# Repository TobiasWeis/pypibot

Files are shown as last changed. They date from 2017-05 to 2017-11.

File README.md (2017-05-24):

# PyPiBot

A robot that is controlled by python on a raspberry pi.
The build is rover-like, with four driven wheels.

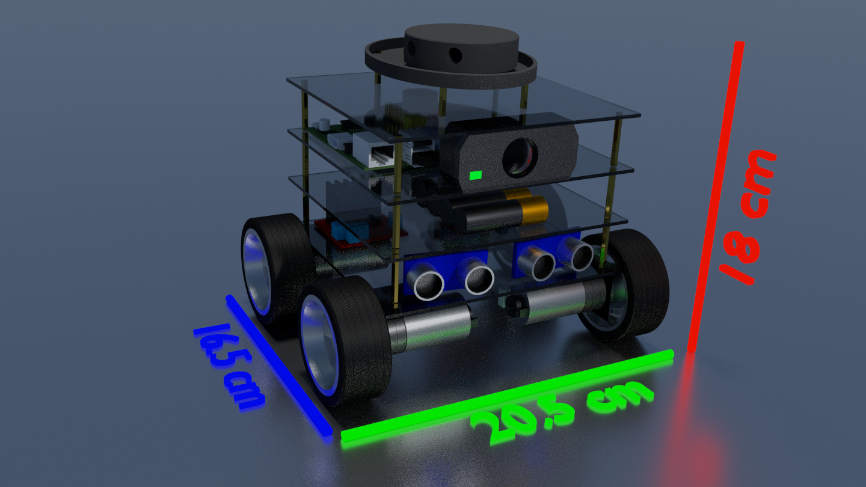
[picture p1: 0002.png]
PyPiBot

<!-- ![PyPiBotGif](./docs/bot.gif) -->

## Parts-List
Whenever available, detailed information and supplier-link are provided as pdf in the docs-folder.
* Raspberry-Pi B+ V2
* Edimax EW-7811UN Wireless USB Adapter

* Motors: 4x DC 6.0V, 35:1 gear ratio, diameter of shaft: 4mm
* Motor-mounts: 4x DROK 25mm universal dc motor mount
* Motor-driver: 2x L298 dual H-bridge modules

* Tires: 4x GoolRC 1:10 Drift Car Tires
* Tire-mount: 12mm Hex Wheel Adapter for 4mm shaft

Current hardware configuration:
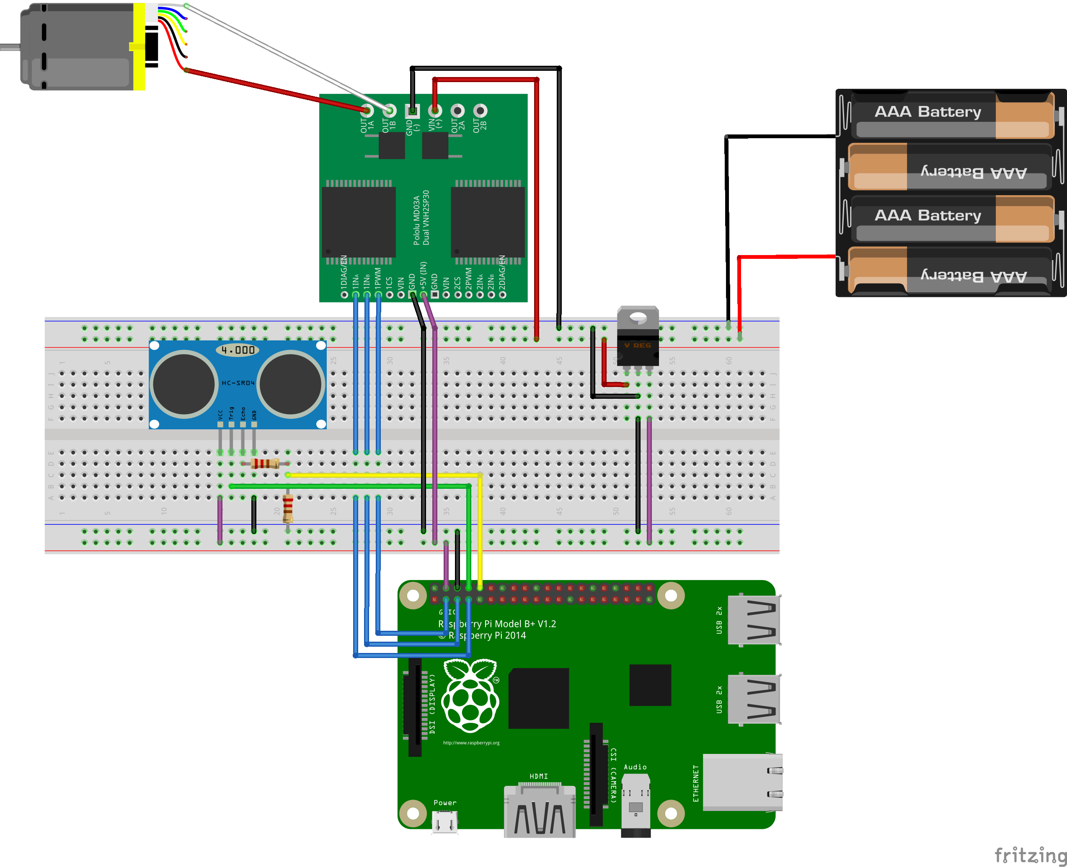
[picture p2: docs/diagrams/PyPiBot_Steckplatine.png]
PyPiBotSchematic


## Software
Basic module structure finished:
* Python mainloop with subprocesses for motor/sensor/worldmodel/reasoning control
* CAM: Sensing: camera + ultrasonic modules
* MEM: Worldmodel: 2D-map of environment
* BRAIN: Reasoning: Obstacle avoidance, object-tracking, self-loading and finding base
* MOT: Motor control: GPIO interfaced with motor-module, speed via PWM-implemention of pyGPIO

TODO:
* Define datatypes and interfaces (messages) for inter-process-communication
* Think about synchronization (in terms of time, perception/action cycle, etc.)
* How to organize perceptions, who marks them as read/removes them from the dictionary?
* Implement logging

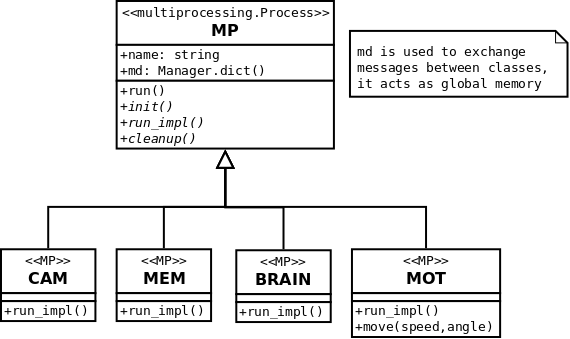
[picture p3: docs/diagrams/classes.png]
Classes


## Setup and Installation

Edimax WLAN-Stick has a power-save mode and goes to sleep, to avoid this:
```
sudo vim /etc/modprobe.d/8192cu.conf
options 8192cu rtw_power_mgnt=0 rtw_enusbss=0
```

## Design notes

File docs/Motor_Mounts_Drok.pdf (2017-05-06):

DROK® 25mm DC Getriebemotor Befestigungswinkel Halter, 4 Stück DC Motor Universal befestigter Halter, schwarz Metall Stand Support Zubehör-Set für 25mm Getriebemotor ( https://www.amazon.de/gp/product/B01MUTDQ0D/ref=oh_aui_detailpage_o00_s00?ie=UTF8&psc=1 (https://www.amazon.de/gp/product/B01MUTDQ0D/ref=oh_aui_detailpage_o00_s00?ie=UTF8&psc=1) )

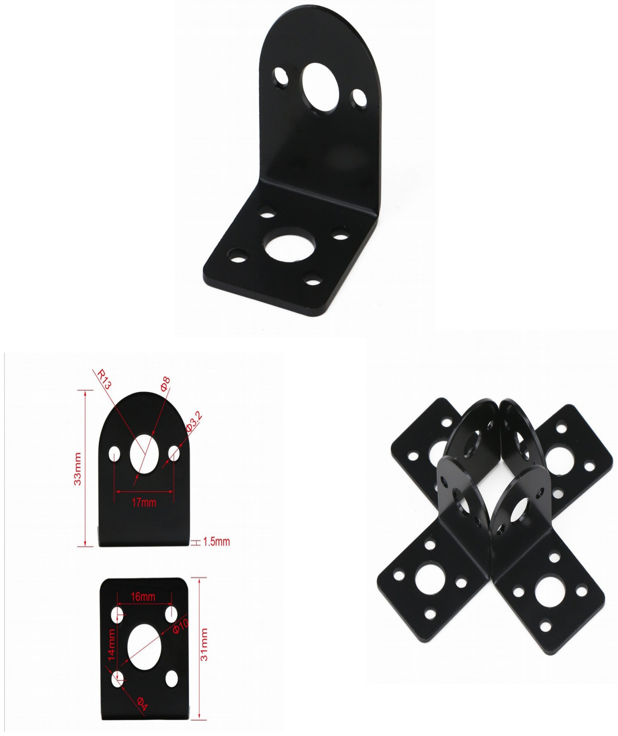
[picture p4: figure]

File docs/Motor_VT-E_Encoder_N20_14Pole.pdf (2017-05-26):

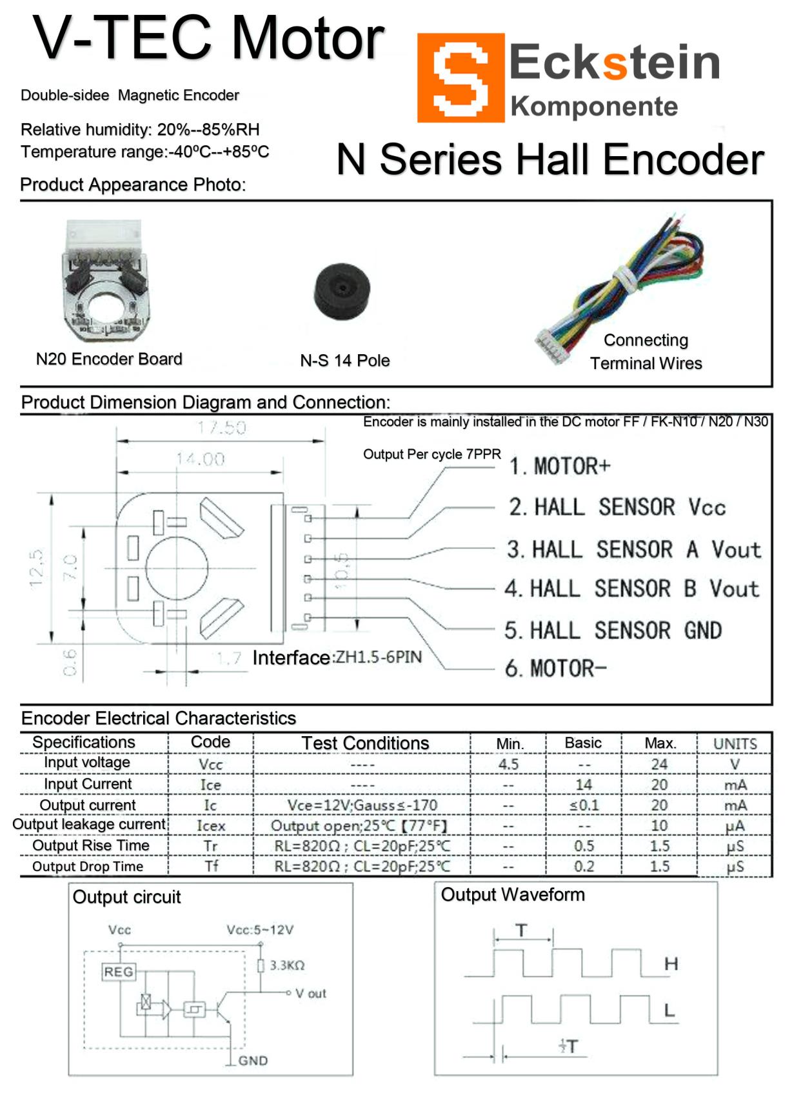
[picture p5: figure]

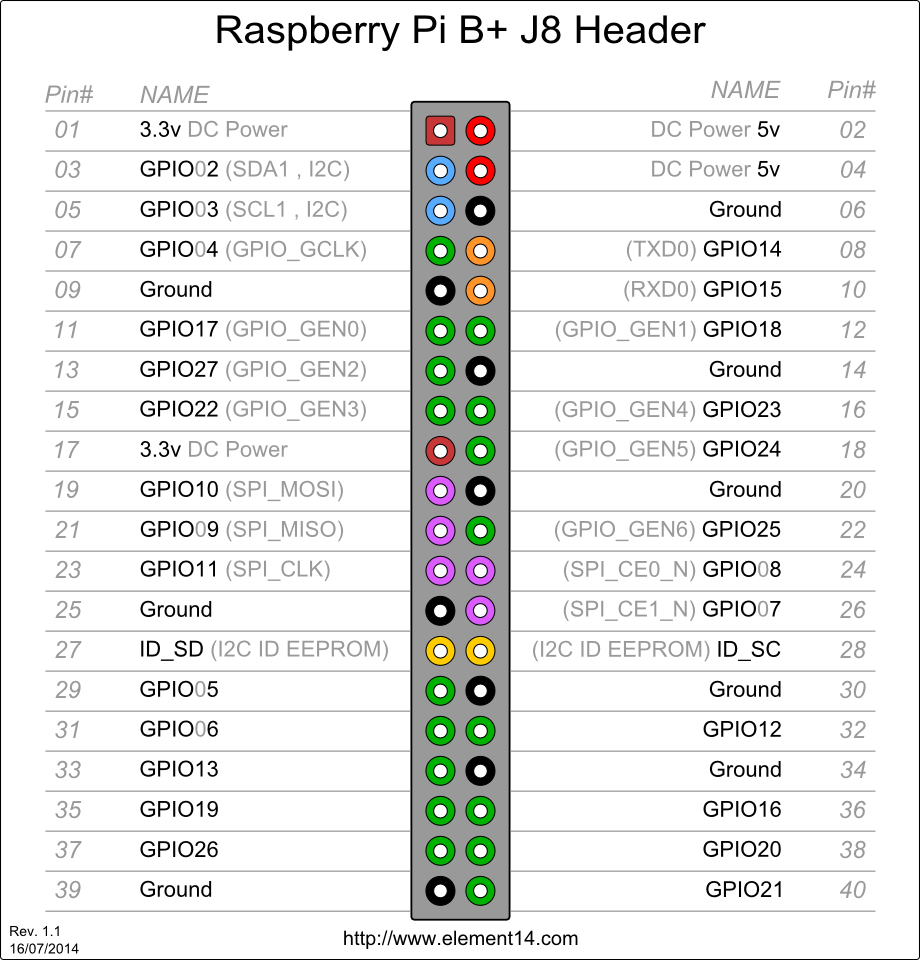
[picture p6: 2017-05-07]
docs/RPi_B+_Pinout.png

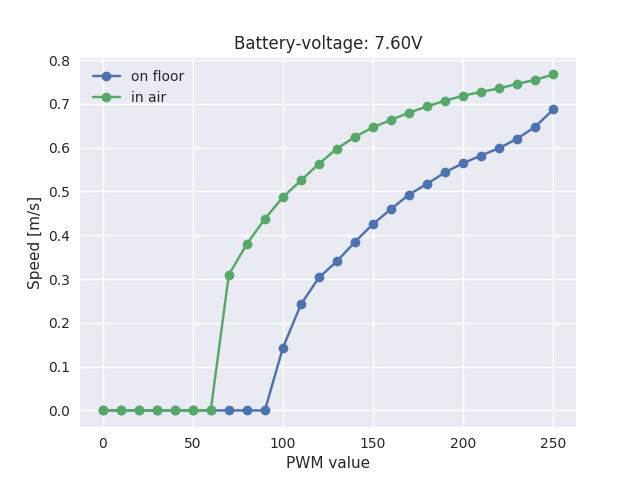
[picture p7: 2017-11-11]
docs/pwm_speeds.png

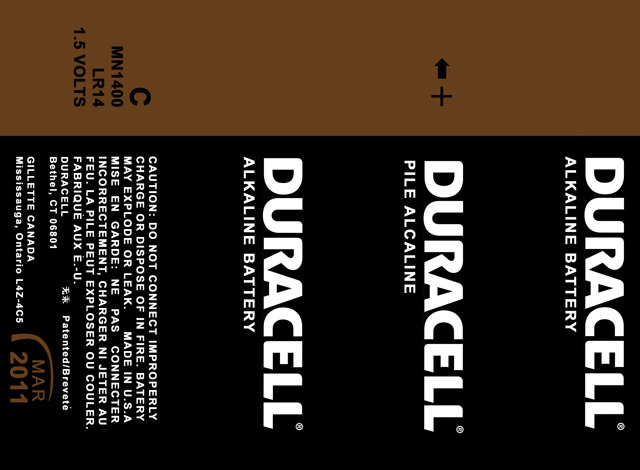
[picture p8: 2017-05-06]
render/c-battery-3d-model-max-obj-3ds-stl-wrl-wrz.jpg

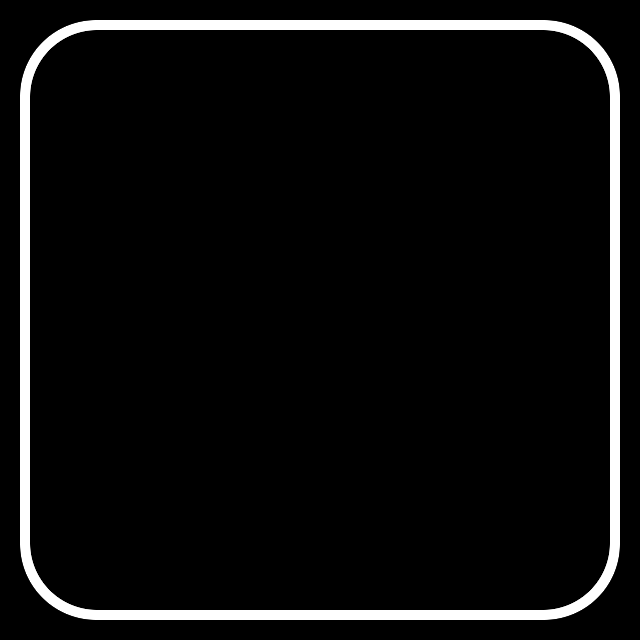
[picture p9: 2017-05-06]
render/TRON_TileX1.png

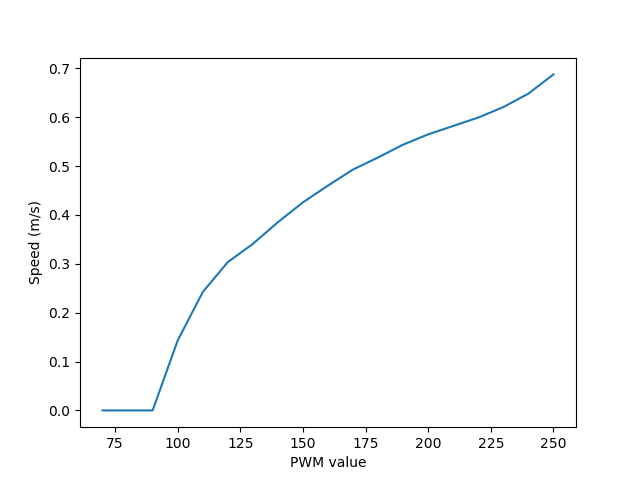
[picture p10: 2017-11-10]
code/prototypes/speeds_on_floor.png

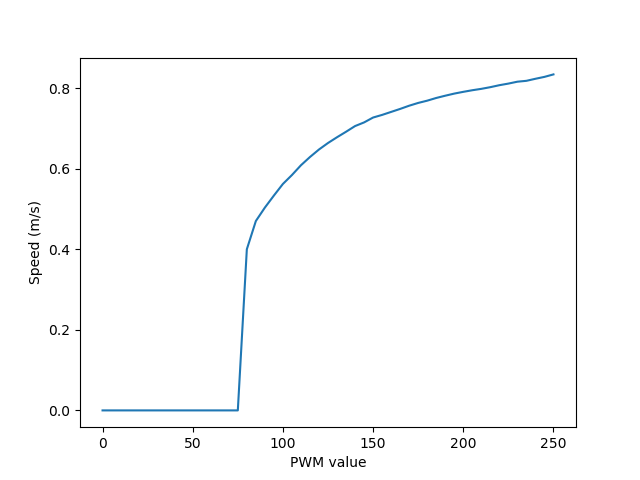
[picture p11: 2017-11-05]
code/prototypes/speeds.png

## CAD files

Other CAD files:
render/Blender_Model_-_Raspberry_Pi_with_Camera_Module/raspberry_pi_with_camera.blend

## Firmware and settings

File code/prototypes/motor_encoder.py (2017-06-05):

#!/usr/bin/python
from threading import Thread
import RPi.GPIO as GPIO
import time
import math

'''
test the wheel encoders
http://guy.carpenter.id.au/gaugette/2013/01/14/rotary-encoder-library-for-the-raspberry-pi/

Motor dreht mit 6200, erste getriebe setzt um auf 177!

6200 U/m -> 103 U/s
177 U/m -> 2.95 U/s

Laut Datenblatt: 14 Pole, 7 Pulse pro U

14 Pole machen doch aber 28 Flanken pro U ?!

-> Bei voller Drehzahl liegen vorne 177 U/s an, hinten 6200 U/s
6200 / 177 == 35.028, d.h. eine volle Umdrehung des Rades NACH Getriebe musste
35.028 * 7 = 245 Pulse haben

Zahle per Umdrehung ca. 1500 Umdrehungen, was ca. 35*14*3 (Ubersetzung, #Pole, Faktor) entspricht (1470))
'''

ENC1A = 32
ENC1B = 36

ENC2A = 38
ENC2B = 40

ENC3A = 18
ENC3B = 22

ENC4A = 12
ENC4B = 16

outfile = open("odo_out.txt", "w+")

class Enc():
    def __init__(self, pina,pinb,name):
        self.a = pina
        self.b = pinb
        self.name = name

        GPIO.setmode(GPIO.BOARD)
        GPIO.setup(self.a, GPIO.IN, pull_up_down=GPIO.PUD_DOWN)
        GPIO.setup(self.b, GPIO.IN, pull_up_down=GPIO.PUD_DOWN)

        self.seq=0
        self.cnt=0
        self.dir=0

        self.ticks_per_round = float(35*14*3)
        #self.circumference = 0.265 # gum tires
        self.circumference = 0.2043 # drift tires

    def get_seq(self):
        a = not GPIO.input(self.a)
        b = not GPIO.input(self.b)

        '''
        Decoder logic
        Seq B   A   A ^ B
        0   0   0   0
        1   0   1   1
        2   1   1   0
        3   1   0   1
        '''
        return (a ^ b) | b << 1

    def reset(self):
        self.cnt = 0

    def check_encoder(self):
        seq = self.get_seq()

        delta = (seq-self.seq) % 4

        if delta == 0:
            pass # nothing happened
        elif delta == 1:
            #print "+",
            #print "%08d - Forward" % cnt # one step
            self.dir = 1
            self.cnt += 1
        elif delta == 2:
            #cnt += 2*direction
            print "X",
            #print "%08d - Two steps" % cnt # clockwise OR counter-clockwise
        elif delta == 3:
            #print "-",
            self.dir = -1
            #print "%08d - Backward" % cnt
            self.cnt -= 1

        self.seq = seq

        return self.seq,self.cnt,self.dir

    def get_travel(self):
        u = self.cnt/self.ticks_per_round 
        m = u*self.circumference
        return m

    def print_track(self):
        u = self.cnt/self.ticks_per_round 
        m = u*self.circumference
        print "%s: %08d\t%d\t%.2f rot, %.3f m" % (self.name, self.cnt,self.dir, u, m)


encoders = [
        Enc(ENC1A, ENC1B, "M1"),
        Enc(ENC2A, ENC2B, "M2"),
        Enc(ENC3A, ENC3B, "M3"),
        Enc(ENC4A, ENC4B, "M4"),
        ]


''' 
Odometry for skid-steered robots: 
https://www.coursera.org/learn/robotics-learning/lecture/YdleV/odometry-modeling

They suggest to SOLELY using a gyro to measure angular change, instead of calculating it from the encoders.
'''

class OdoPosition():
    def __init__(self):
        self.x = 0
        self.y = 0
        self.a = 0

    def integrate(self,tx,ty,ta):
        self.x = self.x + tx*math.cos(self.a) - ty*math.sin(self.a)
        self.y = self.y + tx*math.sin(self.a) + ty*math.cos(self.a)
        self.a = self.a + ta


ss = time.time()
ss2 = time.time()
width_between_wheels = 0.25 #20.5cm
op = OdoPosition()

while True:
    for e in encoders:
        e.check_encoder()

    if time.time() - ss > 0.1: # integrate 10 times a second
        # lets average left ticks for e_inner/e_outer
        e_1_0 = encoders[0].get_travel()
        encoders[0].reset()
        e_1_1 = encoders[1].get_travel()
        encoders[1].reset()
        e_2_0 = encoders[2].get_travel()
        encoders[2].reset()
        e_2_1 = encoders[3].get_travel()
        encoders[3].reset()

        e_1 = (e_1_0 + e_1_1)/2.
        e_2 = (e_2_0 + e_2_1)/2.

        # the larger one is the outer
        e_inner = min(e_1,e_2)
        e_outer = max(e_1,e_2)

        theta = (e_outer - e_inner) / width_between_wheels
        x = ((e_inner + e_outer) / 2) * math.cos(theta)
        y = ((e_inner + e_outer) / 2) * math.sin(theta)
        #print "X: %.2f, Y: %.2f, Theta: %.2f" % (x,y,math.degrees(theta))
        #print e_1_0,",",e_1_1," - ", e_2_0,",",e_2_1
        op.integrate(x,y,theta)
        outfile.write("%.2f, %.2f, %.2f\n" % (op.x, op.y, op.a))
        ss = time.time()

    if time.time() - ss2 > 2:
        print "Position: ", op.x,",",op.y,",",op.a
        ss2 = time.time()

outfile.close()

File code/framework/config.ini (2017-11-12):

[CAM]
DEVICE=0
#WIDTH=1280
#HEIGHT=768
WIDTH=640
HEIGHT=480
FILEPATH=/home/pi/camera_data/

[PINS]
#5
MOTOR1A=3
#3
MOTOR1B=2
#7
MOTOR1E=4
#12
MOTOR1ENCA=18
#16
MOTOR1ENCB=23

#13
MOTOR2A=27
#11
MOTOR2B=17
#15
MOTOR2E=22
#38
MOTOR2ENCA=20
#40
MOTOR2ENCB=21

MOTOR3A=19
MOTOR3B=21
MOTOR3E=23

MOTOR3ENCA=22
MOTOR3ENCB=18

MOTOR4A=29
MOTOR4B=31
MOTOR4E=33

MOTOR4ENCA=16
MOTOR4ENCB=12

US1E=10
US1T=8

BUMPERL=24
BUMPERR=12

[MOT]
# meter per second at pwm 50
MPERS50=0.2
APERS50=5

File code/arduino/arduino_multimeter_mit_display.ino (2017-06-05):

#define sclk 13
#define mosi 11
#define cs   10
#define dc   9
#define rst  8  // y

#include <Adafruit_GFX.h>    // Core graphics library
#include <Adafruit_ST7735.h> // Hardware-specific library
#include <SPI.h>

Adafruit_ST7735 tft = Adafruit_ST7735(cs, dc, rst);

#if defined(__SAM3X8E__)
    #undef __FlashStringHelper::F(string_literal)
    #define F(string_literal) string_literal
#endif

float timestep = 1.f; // save a measuremnt for every timestep
unsigned long last_time = 0; // start time

int sensorPin = A7;
int count = 0; // to measure overall time and set array indices
int ofy = 140; // y-offset for values and scales
int scale=8; // scaling of pixels/volt
float values[128];

/*
void testdrawtext(String text, uint16_t color, uint16_t tsize) {
  tft.setCursor(0, 0);
  tft.setTextSize(tsize);
  tft.setTextColor(color, ST7735_BLACK); // second color is background, overwrite!
  tft.setTextWrap(true);
  tft.print(text);
}
*/

void setup(){
  tft.initR(INITR_REDTAB);
  tft.fillScreen(ST7735_BLACK);
  // creates the 0/10-lines and clears measurement area
  setup_measurements();
  Serial.begin(115200);
}

float getVoltage(){
  int sensorValue = analogRead(sensorPin);
  return sensorValue * (10.0 / 1023.);
  
}

void setup_measurements(){
  // create the bottom line and text  
  tft.setCursor(0, ofy+3);
  tft.setTextSize(1);
  tft.print("0 V, ");  
  tft.drawLine(0, ofy+1, tft.width()-1, ofy+1, ST7735_WHITE);
  
  // create top-line and text
  tft.setCursor(0, ofy-10*scale-1-10);
  tft.setTextSize(1);
  tft.print("10 V");
  tft.print(", t-step: ");
  tft.print(timestep);
  tft.print(" s");
  tft.drawLine(0, ofy-10*scale-1, tft.width()-1, ofy-10*scale-1, ST7735_WHITE);
}

void printVoltage(float volt, uint16_t color, uint16_t tsize){
  tft.setCursor(0, 0);
  tft.setTextSize(1);
  tft.setTextColor(color, ST7735_BLACK); // second color is background, overwrite!
  tft.setTextWrap(true);
  tft.println("Voltage: ");
  tft.println();
  
  tft.setTextSize(tsize);
  tft.println(volt);
}

void loop(){
  float volt = getVoltage();
  printVoltage(volt, ST7735_WHITE, 3);
  
  if (millis() - last_time >= timestep*1000){
    Serial.println(volt, 4);

    if (count >= tft.width()-1){
      // shift all array elements to the left, replace last value
      for(int k=0; k<127;k++){
        // paint all old pixels black instead of drawing complete lines
        tft.drawPixel(k, ofy-scale*values[k], ST7735_BLACK);
        values[k] = values[k+1];
        tft.drawPixel(k, ofy-scale*values[k], ST7735_GREEN);        
      }
      values[127] = getVoltage();
    }else{
      values[count] = getVoltage();
      tft.drawPixel(count, ofy-scale*values[count], ST7735_GREEN);        
    }
    count = count + 1;
    
    // draw elapsed time
    tft.setCursor(25, ofy+3);
    tft.setTextSize(1);
    tft.print(count*timestep);
    tft.print(" s");

    last_time = millis();    
  }
}

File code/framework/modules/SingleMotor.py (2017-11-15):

#import RPi.GPIO as GPIO
import pigpio
from utils import *
import collections

class SingleMotor():
    def __init__(self,a,b,e,enca,encb,name,use_pid=True):
        self.a = a
        self.b = b
        self.e = e
        self.enca = enca
        self.encb = encb
        self.name = name
        self.use_pid = use_pid

        self.lasta = -1
        self.lastb = -1

        self.pi = pigpio.pi()

        self.pi.set_mode(self.a, pigpio.OUTPUT)
        self.pi.set_mode(self.b, pigpio.OUTPUT)
        self.pi.set_mode(self.e, pigpio.OUTPUT)

        self.pi.set_mode(self.enca, pigpio.INPUT)
        self.pi.set_mode(self.encb, pigpio.INPUT)
        self.pi.set_pull_up_down(self.enca, pigpio.PUD_UP)
        self.pi.set_pull_up_down(self.encb, pigpio.PUD_UP)

        # configure callbacks
        self.cba=self.pi.callback(self.enca, pigpio.EITHER_EDGE, self.get_state)
        #self.cbb=self.pi.callback(self.encb, pigpio.EITHER_EDGE, self.get_state)

        self.set_mode("release")
        self.speed_ms = 0

        # set up variables for encoder comptuations
        self.old_seq = 0
        self.direction = 0
        self.cnt = 0

        self.PID_UPDATE_INT_MS = 50
        self.pid_ts = getMs()
        self.pid_queue = collections.deque()
        self.pid_kp = 3.0
        self.pid_ki = 0.7
        self.pid_kd = 0.0
        self.pid_last_error = 0.
        self.pid_integral = 0.

        # setup PWM on enable port
        self.pi.set_PWM_dutycycle(self.e, 0)
        
        # FIXME: remove
        self.outfile = open("/tmp/pid_out_%s_%.2f_%.2f_%.2f.txt" % (self.name, self.pid_kp, self.pid_ki, self.pid_kd), "w")
        self.outfile.write("HEADER: Kp: %f, Ki: %f, Kd: %f\n" % (self.pid_kp, self.pid_ki, self.pid_kd))
        self.outfile.write("HEADER: tsnow, tmpdelta, err, self.pid_integral, deriv, out, out_pwm, dt, speed_ms\n")


    def set_mode(self, d):
        if d == "backward":
            self.direction=-1
            self.pi.write(self.a, 1)
            self.pi.write(self.b, 0)
        elif d == "forward":
            self.direction=1
            self.pi.write(self.a, 0)
            self.pi.write(self.b, 1)
        elif d == "block":
            self.pi.write(self.a, 1)
            self.pi.write(self.b, 1)
        elif d == "release":
            self.pi.write(self.a, 0)
            self.pi.write(self.b, 0)
        else:
            print "Motor: I do not know this direction"

    def get_seq(self):
        a = not self.pi.read(self.enca)
        b = not self.pi.read(self.encb)
        return (a ^ b) | b << 1

    def get_state(self, gpio, level, tick):
        curr = getMs()
        if level == 1:
            self.cnt += self.direction*1
            if self.use_pid:
                self.pid_queue.append(curr) # push ts in a queue 

        if self.use_pid:
            for elem in list(self.pid_queue): # remove elements from queue that are older than 100Ms
                if curr - elem > self.PID_UPDATE_INT_MS:
                    self.pid_queue.popleft()
                else:
                    break

            # PID loop
            dt = curr - self.pid_ts
            if dt >= self.PID_UPDATE_INT_MS:
                #print "[",self.name,"] (",len(self.pid_queue),") Queue: " #, self.pid_queue
                #print "[",self.name,"] DIFF: ", (curr - self.pid_ts)
                # calculate speed in m/s over the last 100Ms
                tmpdelta = self.cnt_to_m(len(self.pid_queue)) # this is the distance of the last 100Ms
                #print self.speed_ms,"-",tmpdelta*(1000./float(self.PID_UPDATE_INT_MS)), "-", self.speed_ms - tmpdelta*(1000./float(self.PID_UPDATE_INT_MS))
                err = self.speed_ms - tmpdelta*(1000./float(dt))
                self.pid_integral += err
                self.pid_integral = min(2.0, max(-2.0, self.pid_integral))
                deriv = (err - self.pid_last_error)
                out = self.pid_kp*err + self.pid_ki*self.pid_integral + self.pid_kd*deriv

                # translate "out"-value (m/s) to pwm value
                #if out < 0: out = 0.0
                if out > 0.7: out = 0.7

                if out <= 0:
                    out_pwm = 0 # if we fall below the threshold, there is anyway zero output
                else:
                    out_pwm = min(255, max(0, int(64.46*out*out*out + 310.2*out*out - 2.388*out + 41.16)))


                tsnow = getMs()
                self.outfile.write("%d, %f, %f, %f, %f, %f, %d, %d, %f\n" % (tsnow, tmpdelta, err, self.pid_integral, deriv, out, out_pwm, dt, self.speed_ms))

                #print "[",self.name,"]-------------------PID: delta: ",tmpdelta*(1000./self.PID_UPDATE_INT_MS),", err: ",err,", out: ", out, ", out_pwm: ", out_pwm
                self.pid_last_error = err
                self.pi.set_PWM_dutycycle(self.e, out_pwm)
                self.pid_ts = curr

    def check_encoder(self):
        '''
        here for legacy reasons
        '''
        seq = self.get_seq()
        delta = (seq - self.old_seq) % 4
        self.old_seq = seq

        if delta == 0:
            pass # nothing happened
        elif delta == 1:
            self.cnt += 1
        elif delta == 2:
            self.cnt += 2*self.direction
        elif delta == 3:
            self.cnt -= 1

    def cnt_to_m(self,cnt):
        return (cnt/float(350))*0.26 # circumference

    def get_delta(self):
        '''
        called from outside.
        cnt updated through interrupts and callback to get_state
        '''
        #self.check_encoder()
        delta_m = self.cnt_to_m(self.cnt) 
        self.cnt = 0
        return delta_m

    def set_speed(self,speed):
        '''
        with the PID, this speed should be in m/s
        '''
        self.speed_ms = speed
        self.get_state(0,0,0)
        #self.pi.set_PWM_dutycycle(self.e, speed)
        #self.p.ChangeDutyCycle(speed)

    def cleanup(self):
        self.pi.set_PWM_dutycycle(self.e, 0)
        self.set_mode("release")
        self.cba.cancel()
        #self.cbb.cancel()
        self.outfile.close()

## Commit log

2017-05-06 initial checkin
    [raspberry_pi_with_camera.blend]
2017-05-07 fix in prototype gpio, implementation of basic framework
    [BRAIN.py, MOT.py, MP.py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]
2017-05-07 added Fritzing diagram
    [PyPiBot.fzz]
2017-05-07 added prototype code for hc-sr04 ultrasonic sensor
2017-05-07 included HC-SR04 in schematic
    [PyPiBot.fzz]
2017-05-08 added class for single motor
2017-05-08 added gitignore, modified motor class
2017-05-08 added ultrasonic (US) module and reaction in brain
2017-05-14 designed fritzing part for motor with encoder, updated diagram
    [PyPiBot.fzz]
2017-05-22 updated renderings to current robot platform
    [PyPiBot.fzz]
2017-05-24 manual motor control
2017-05-24 start of dead-reckoning, implemented four motors
2017-05-24 minor fixes, implemented test-routing in brain to test motor functions
    [BRAIN.py, MOT.py, US.py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]
2017-05-25 minor modifications, added prototype script to read hall-encoders of motors
2017-05-26 added datasheet for encoders
2017-05-26 minor changes to test motor encoders, integrated wheel circumference
2017-05-28 start of encoder integration
2017-06-03 added script to capture camera images
2017-06-04 encoder-script refactor and integration of all four quadrature encoders
2017-06-04 started skid-steer model
2017-06-05 added arduino udev-rule and code to read voltage
2017-06-05 added arduino code for voltage-reading
2017-06-06 laserscanner experiments...only 3Hz output instead of 5
2017-06-08 added lidar live view script, minor changes on modules
2017-06-08 solved LIDAR timing issues
    [LIDAR.py]
2017-09-10 implemented lidar simulator
2017-09-10 simulation with lidar and mcs integration works now
2017-09-10 minor fixes to simulation
    [SIMU.py, config.ini]
2017-09-23 Fixed simulated laserscanner, simulation fully working now
    [BRAIN.py, MAP.py, SIMU.py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]
2017-10-01 simulate single motors instead of integration for more reality
2017-10-05 new manual mode with curses and for only two motors
2017-10-05 checking in LIDAR module again
2017-10-29 minor on odometry
2017-10-29 fixed odometry
2017-10-31 recoded encoder, using pigpio with interrupts now
2017-10-31 corrected constants for delta calculations
    [SingleMotor.py]
2017-11-04 start of pid control
2017-11-05 script to measure pwm/speed relation and plot
2017-11-11 new plots, implemented m/s to pwm mapping for PID
2017-11-13 further work pid...still needs more tuning
2017-11-13 added plotting for pid
2017-11-13 pid seems to be stable, evade behavior needs fix
    [BRAIN.py, LIDAR.py, SingleMotor.py]
2017-11-15 pid seems stable now
